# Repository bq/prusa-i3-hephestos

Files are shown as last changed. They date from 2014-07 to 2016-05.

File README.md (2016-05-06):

Prusa i3 Hephestos
======

In this repository you will find the source files for the [Prusa i3 Hephestos 3D printer](http://www.bq.com/es/productos/prusa-hephestos.html). If you are missing something, please do not hesitate to [file an issue on github](http://www.bq.com/es/productos/prusa-hephestos.html).

License 
======

Prusa i3 Hephestos is licensed under a [Creative Commons Attribution-ShareAlike 4.0 International License](http://creativecommons.org/licenses/by-sa/4.0/)

Firmware
===================

Sources on GitHub: https://github.com/bq/Marlin

Attributions
============
 
 - Josef Prusa: 
  - Prusa i3 3D printer original author.
 - Juan Gonzalez Gómez (Obijuan):
  - Desing "Final de carrera Eje X" and FreeCAD parts migration.
 - Manuel Palacios:
  - PowerCode 3D printer author. A lot of parts from this printer are used in Hephestos and derived("Eje X Carro A", "Anclaje del motor izquierdo del Eje Z", "Eje X izquierda").
 - Pedro de Oro Martín:
  - Desing; "Acople cadeneta Eje X", "Sujección final de carrera Eje Z", "Seguridad Hot End", "Soporte Ventilador", "Llave fija impresa".
 - Antonio Castro Gómez: 
  - Desing; "Sujección final de carrera Eje Y", "Soporte para filamento".
 - Jose Emilio Torres:
  - Desing "Soporte LCD".

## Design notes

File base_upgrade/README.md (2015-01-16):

Prusa i3 20x30cm bed upgrade kit
======

In this repository you will find the source files for the [Prusa i3 20x30cm bed upgrade kit](http://diwo.bq.com/amplia-tu-prusa-con-el-kit-de-actualizacion-a-base-larga/). If you are missing something, please do not hesitate to [file an issue on github](http://www.bq.com/es/productos/prusa-hephestos.html).

License 
======

Prusa i3 20x30cm bed upgrade kit is licensed under a [Creative Commons Attribution-ShareAlike 4.0 International License](http://creativecommons.org/licenses/by-sa/4.0/)

Attributions
============
 
 - Pedro de Oro Martín:
  - Kit author, Design drawings with LibreCAD , printed parts in OpenSCAD and modifications of parts pieces in OpenSCAD.
 - Josef Prusa:
  - Prusa i3 3D printer original author.
 - Manuel Palacios:
  - PowerCode 3D printer author of which have been derived parts; "Frontal de aluminio", "Tensor".
 - GalaCC authors:
  - Of which have been derived parts; "Posterior de aluminio", "Sujeta motor Y", which in turn have been derived from PowerCode 3D printer.
 - Federico Figueiredo de Sousa:
  - Author of the rendered images.

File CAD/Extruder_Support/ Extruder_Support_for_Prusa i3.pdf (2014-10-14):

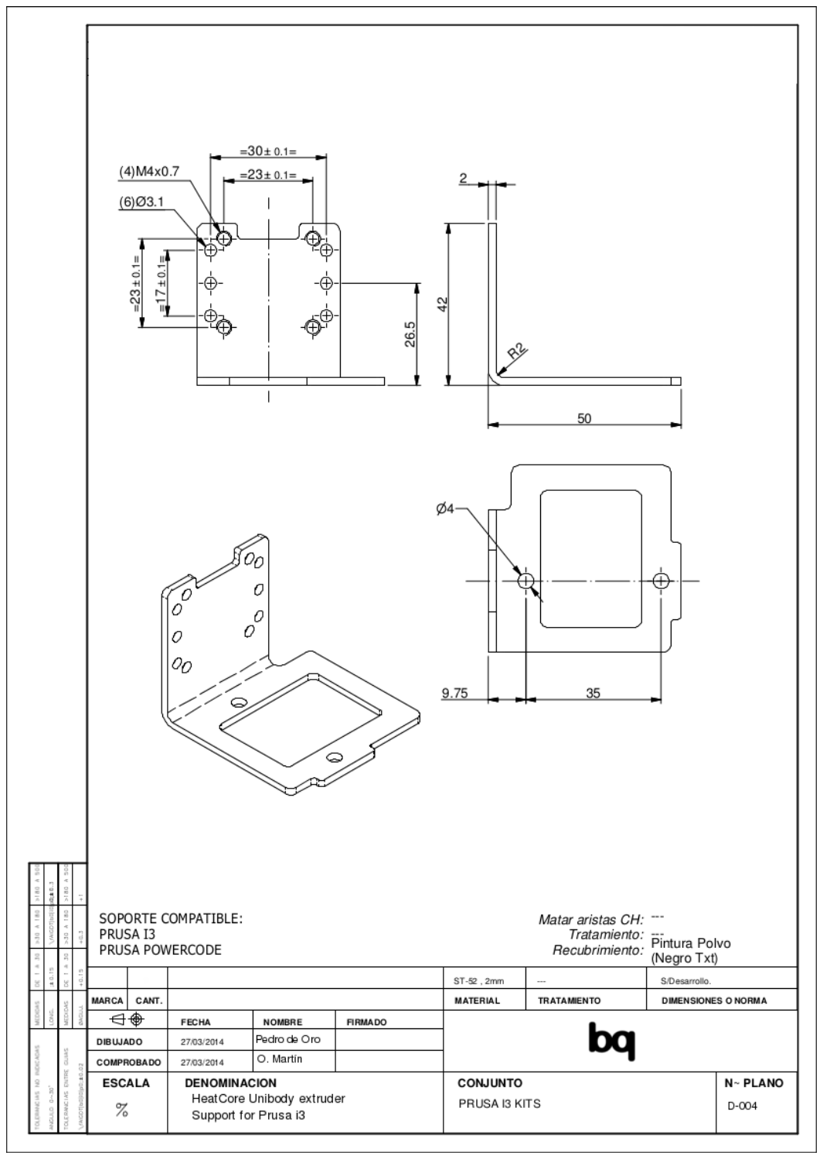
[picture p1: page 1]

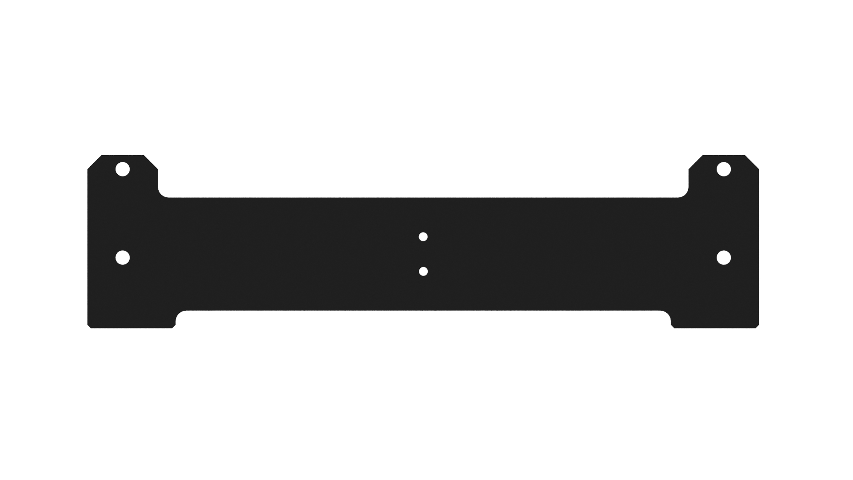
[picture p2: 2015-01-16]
base_upgrade/media/Posterior de Aluminio.jpg

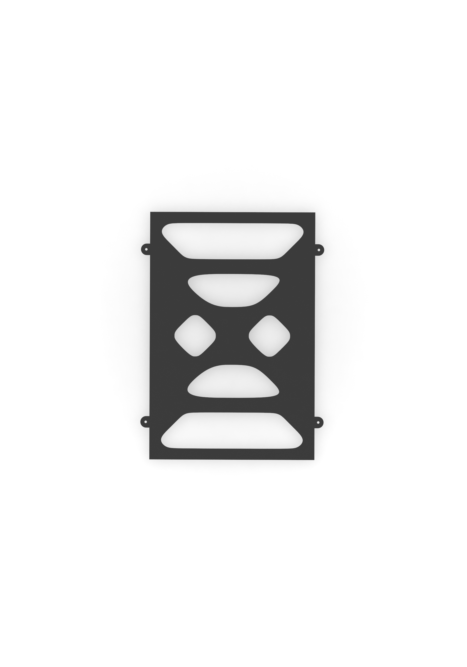
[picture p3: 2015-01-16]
base_upgrade/media/metacrilato.jpg

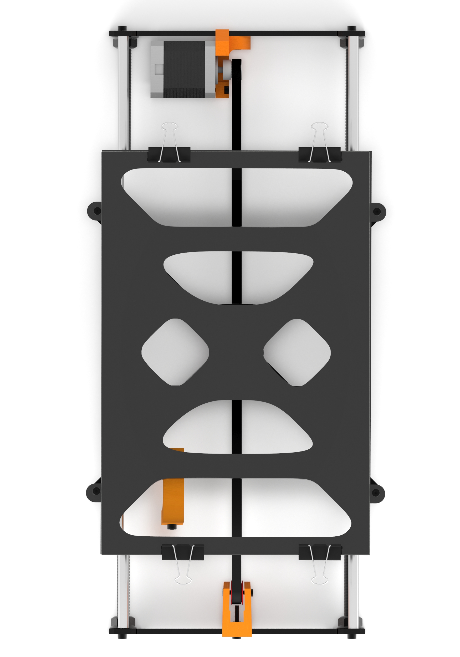
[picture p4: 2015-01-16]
base_upgrade/media/Base_larga_top.jpg

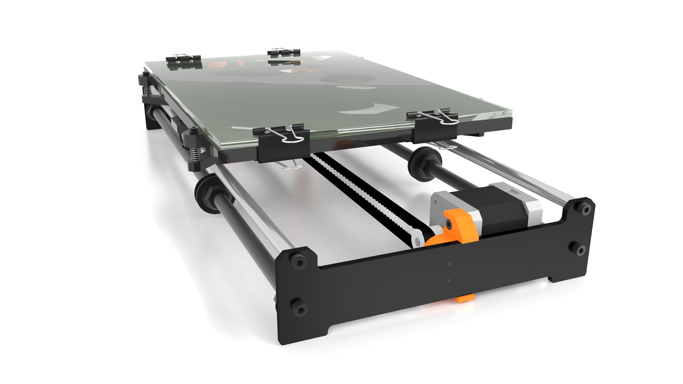
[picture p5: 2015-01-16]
base_upgrade/media/Base_larga_04n.jpg

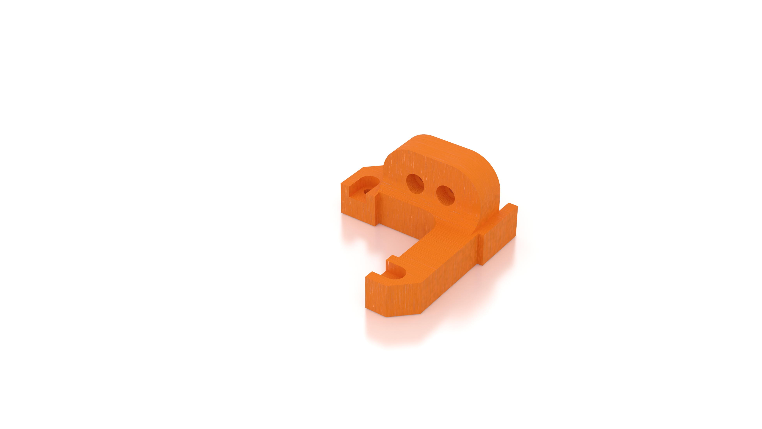
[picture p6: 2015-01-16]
base_upgrade/media/Pieza fijadora 2.jpg

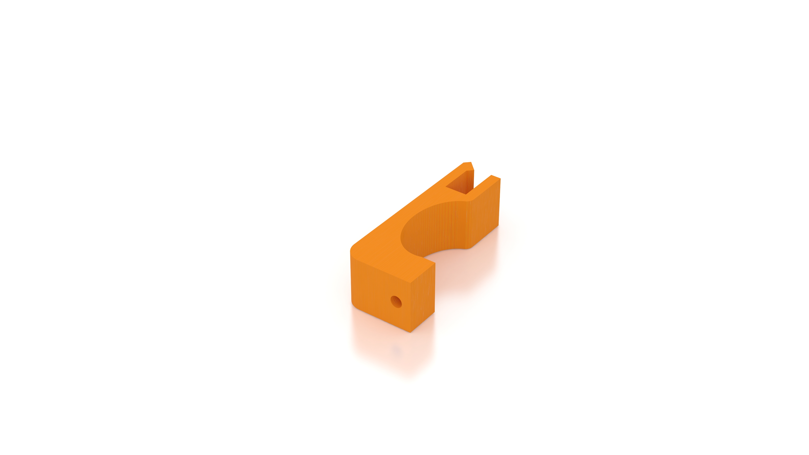
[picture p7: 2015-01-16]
base_upgrade/media/End-stop.jpg

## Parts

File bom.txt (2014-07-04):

BOM Prusa i3 Hephestos
======================

-----------Name------------------------------------------------------Quantity--

Allen key s/long Ø 2mm	                                                 1
ALLEN KEY S/LONG Ø2,5 FORUM	                                         1
Ceramic screw driver trimmer for electronics	                         1
Precision Needle 0.4mm diameter	                                         2
Printed tools: spanner and holder	                                 1
Ramps 1.4 Kit	                                                         1
Stepstick Drivers A49988 4 layers	                                 4
Mechanical Endstop	                                                 3
Smart LCD Controller	                                                 1
USB Cable 1.8m A-B	                                                 1
4 wire red blue green black (1 meter) for RAMPS	                         4
Nema 17 48 mm sin conector 42BYGHW811	                                 4
bq Direct Drive Extruder wiring kit 150 cm length	                 1
Bi-colour wire 2 x 1,5 mm	                                         0,15
AC/DC Power Adaptor SA1208 - 12V DC - 8A with 2.1mm Jack Connector	 1
SCHURTER 6003.0215 - Cable;	                                         1
2.1mm female Jack connector to two wires clam	                         1
Printed support for lcd, ramps and fan	                                 1
Tornillo M3x12 Screw - DIN-912 8.8 Class Black	                         4
M3 Nut - DIN 934 Class 8 Black	                                         38
Heat shrink tube 2.5 x 500 mm	                                         0,5
Black bridle 100 x 2.5 mm	                                         28
Brushless DC Cooling Fan - RD5010B12H	                                 1
Plastic Drag Chain Link 15x35 mm	                                 52
Marcha Direct Drive Extruder 1.75mm 0.4mm for RepRap Printers	         1
Witbox extruder Support for Prusa i3	                                 1
Tornillo M4 x 6 Din 7984	                                         2
M3x10 Screw - DIN-912 Class 8.8 Black	                                 35
Tornillo M3 x16 Screw - DIN-912 8.8 Class Black	                         8
M3x18 Screw - DIN-912 Class 8 Black	                                 2
Ø8X370MM-CROMAD Smooth rod	                                         2
M3x20 Screw - DIN-912 Class 8 Black	                                 9
Tornillo M3x25 Screw - DIN-912 8.8 Class Black	                         8
M6x40 Screw - DIN-912 Class 8.8 Black	                                 1
M5 Nut - DIN 934 Class 8 Black	                                         4
M6 Nut - DIN 934 Class 8 Black	                                         3
Printed x axis for Prusa i3	                                         1
Axial Ball Bearing 623zz	                                         2
GT2 Pulley 20 dientes	                                                 2
GT2 Timing Belt 6mm	                                                 2
Linear Ball Bearing LM8uu	                                         10
Ø8X340MM-CROMAD Smooth rod	                                         2
M10X370MM-NE Threaded rod	                                         2
M8X205MM Black transversal rod	                                         4
M8 Nut - DIN 934 Class 8 Black	                                         22
M10 Nut - DIN 934 Class 8 Black	                                         12
M8 Washer - DIN-125 Class 6 Black	                                 22
M10 Washer - DIN-125 Class 6 Black	                                 12
Printed y axis for Prusa i3	7
Aluminium Prusa i3 Frame and Bed 6mm black	1
22 x 22 x 10 mm acrylic printing bed for RepRap Printers	1
Standard Spring 30.5x4.5x0.45	4
Black binder clip	4
Ø8X320MM-CROMAD Smooth rod	2
M5X300MM-NE Threaded rod	2
Aluminium Flexible Shaft Coupling 5to5	2
Printed z axis for Prusa i3	
Glass 3mm 220x220 4EC 20x20	1
Jumper Wire (3 wires) with connectors – 40 cm	2
Jumper Wire (3 wires) with connectors – 85 cm	1
Hot End security	1
M10  Serrated Nut DIN 6923 Class 8 black	4
M10 Washer DIN 9021 Black (outter diameter 30mm)	4
Wire ferrule 1,5mm	4

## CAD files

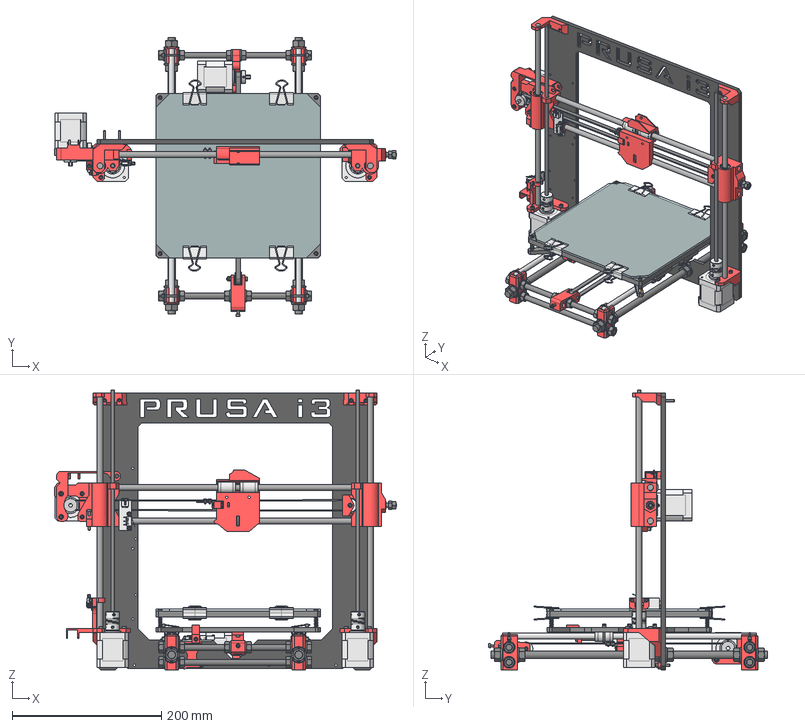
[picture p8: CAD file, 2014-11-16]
freecad/prusa-hephestos-assembly.fcstd
457.6 x 373.7 x 374.0 mm
M3x20-hex-bolt
M8-washer-tensor-1
M8-washer-tensor-2
M8-nut-tensor-1
M8-nut-tensor-2
belt-guide
M3-nut-y-tensor-003
M3-nut-y-tensor-2
M3x25-hex-bolt-1
M3-nut-y-tensor-1
y-idler-tensioner-final
y-Pulley-GT2
M3x10-bolt-motor-1
M3x10-bolt-motor-002
M3x10-bolt-motor-003
M3-setscrew-y-motor
y-Nema-17_Stepper_Motor_47mm
y-motor-plate
M8-washer-motor-1
M8-washer-motor-002
M8-washer-motor-003
M8-washer-motor-004
M8-nut-motor-1
M8-nut-motor-002
M8-nut-motor-003
M8-nut-motor-004
M10x370mm-left
M10x370mm-right
M8x340-smooth-rod-y-left
M8x340-smooth-rod-y-right
M8-washer-1
M8-washer-2
M8-washer-003
M8-washer-004
M8-washer-005
M8-washer-006
M8-washer-007
M8-washer-008
M8-washer-009
M8-washer-010
M8-washer-011
M8-washer-012
M8-washer-013
M8-washer-014
M8-washer-015
M8-washer-016
Washer-M10
Washer-M011
Washer-M012
Washer-M013
Washer-M014
Washer-M015
Washer-M016
Washer-M017
M8-nut-1
M8-nut-002
M8-nut-003
M8-nut-004
M8-nut-005
M8-nut-006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

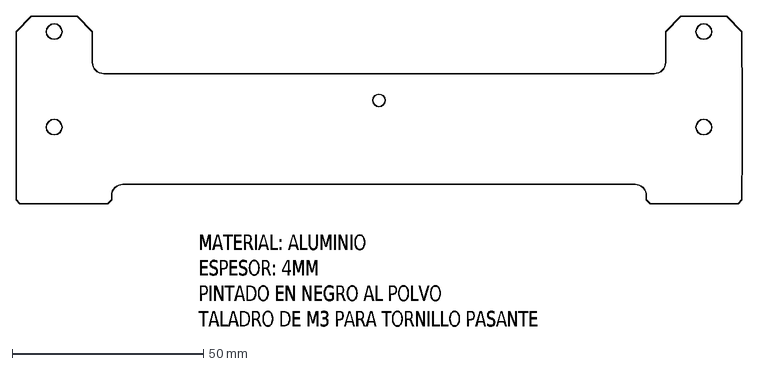
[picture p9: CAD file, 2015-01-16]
base_upgrade/DXF/Frontal_Alumino_4mm_Negro.dxf
MATERIAL: ALUMINIO ESPESOR: 4MM PINTADO EN NEGRO AL POLVO TALADRO DE M3 PARA TORNILLO PASANTE

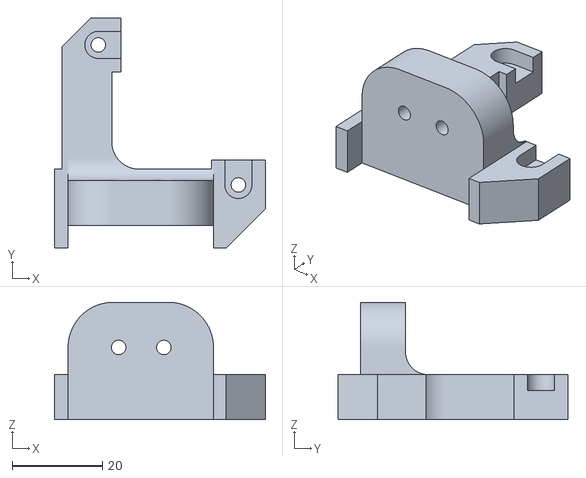
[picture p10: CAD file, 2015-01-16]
base_upgrade/STL/Sujeta_motor_base larga.stl
46.7 x 51.0 x 26.0

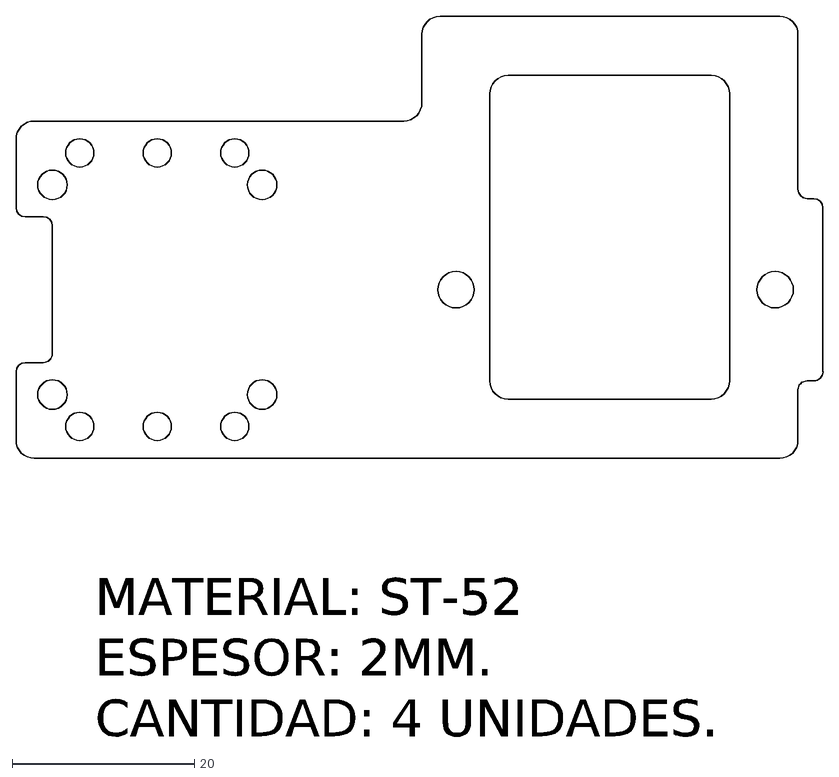
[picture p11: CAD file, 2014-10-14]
CAD/Extruder_Support/Extruder_Support_for_Prusa_i3.dxf
MATERIAL: ST-52 ESPESOR: 2MM. CANTIDAD: 4 UNIDADES.

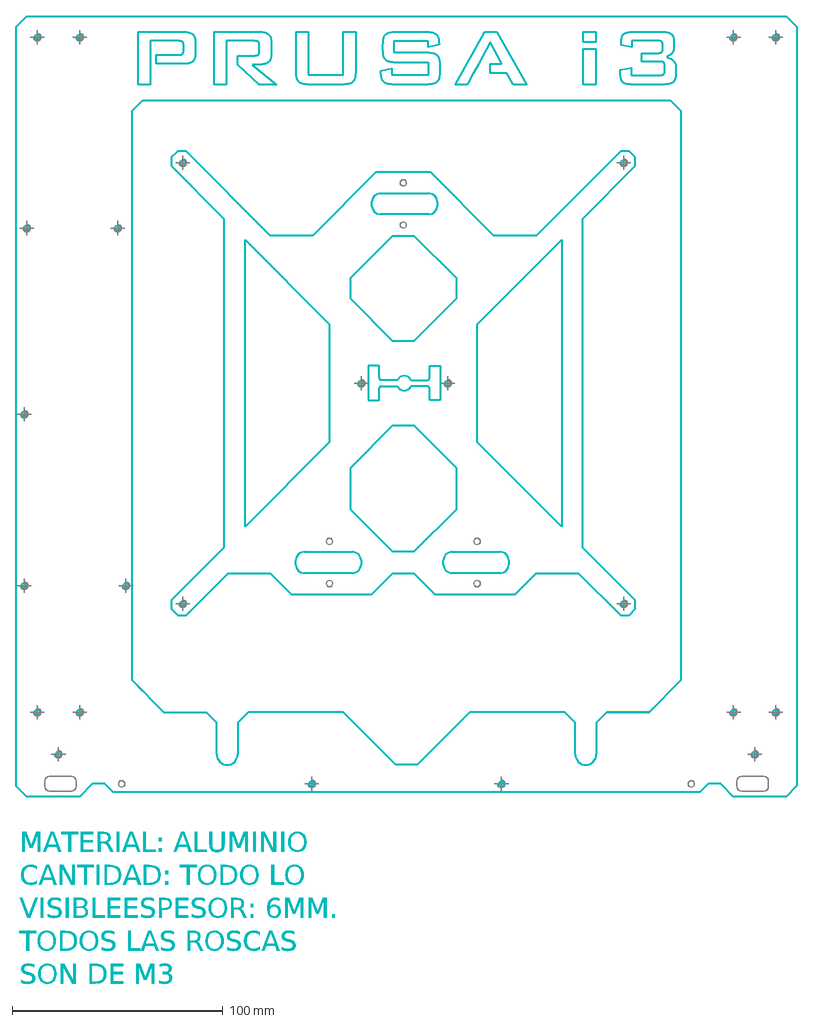
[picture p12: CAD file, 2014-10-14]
CAD/Frame&base/Frame&base_Hephestos_V2.dxf
MATERIAL: ALUMINIO CANTIDAD: TODO LO VISIBLE ESPESOR: 6MM. TODOS LAS ROSCAS SON DE M3

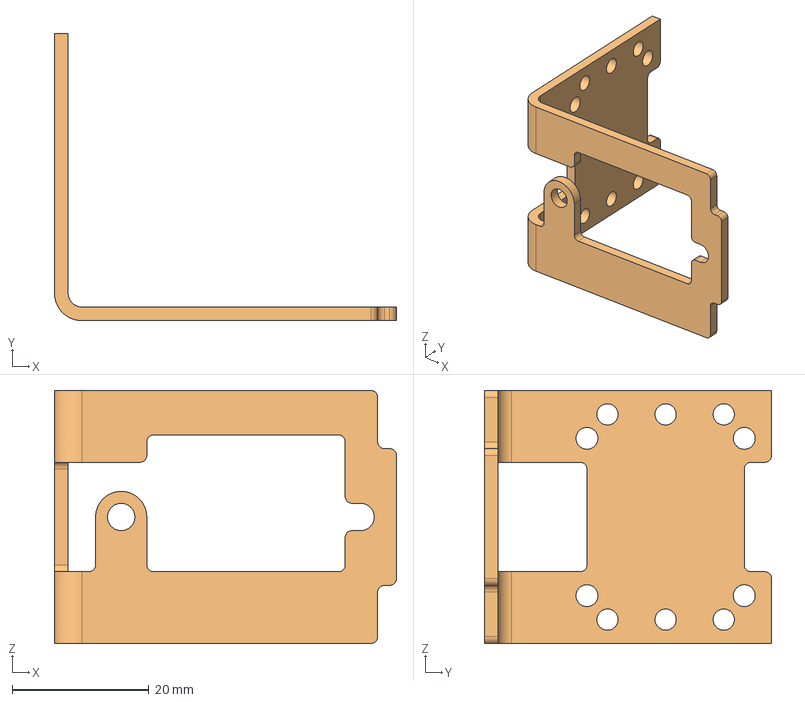
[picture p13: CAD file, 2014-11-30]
freecad/non-printable-parts/extruder-support.fcstd
50.0 x 42.0 x 37.0 mm
drills
extruder-support-final

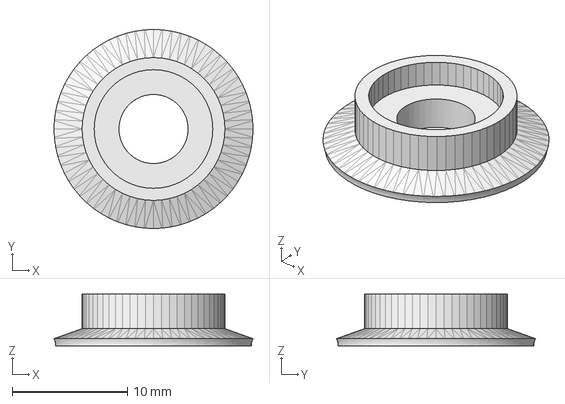
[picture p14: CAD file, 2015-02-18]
freecad/polea_V2.FCStd
17.3 x 17.3 x 4.50 mm

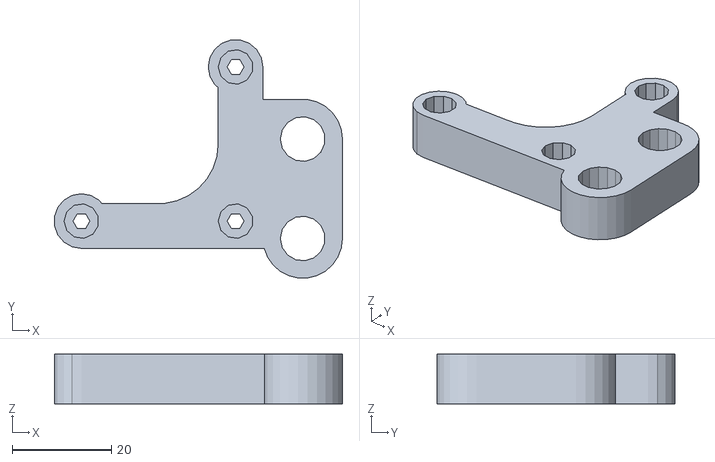
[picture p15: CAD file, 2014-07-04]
scad/Eje_Y/reinforced_y-motor/y-motor_mirror.stl
57.9 x 47.9 x 10.0

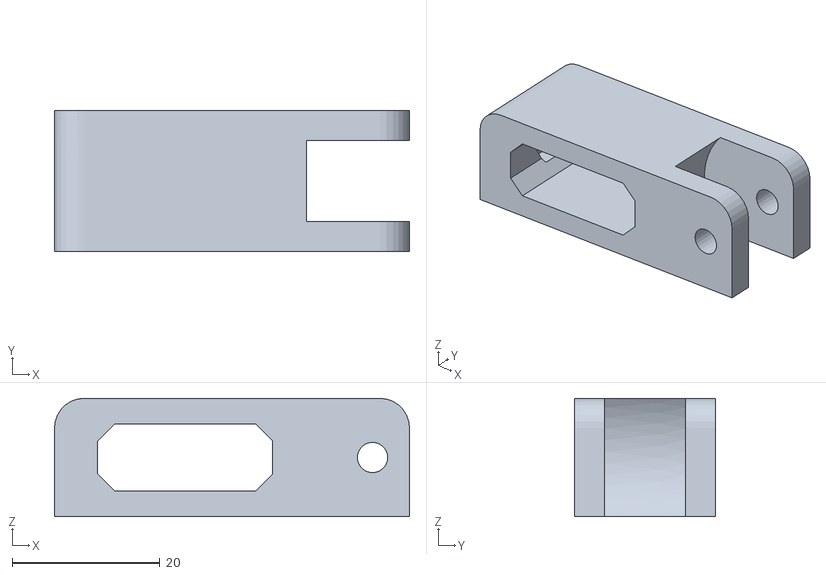
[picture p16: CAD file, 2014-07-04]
scad/Eje_Y/Y_tensor_correa/i3_y-idler_with_tensioner/i3_y-idler_with_tensioner/y-idler-tensioner3-4mm.stl
48.0 x 19.0 x 16.0

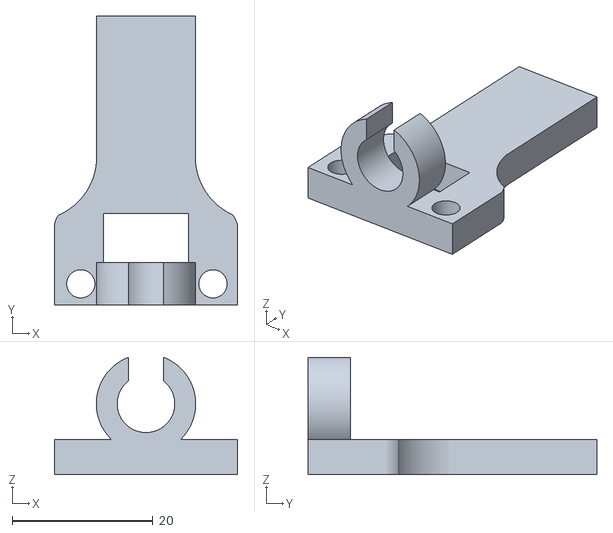
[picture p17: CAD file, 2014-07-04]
scad/Eje_Z/Final_de_carrera_eje Z/Eje_Z_final_carrera.stl
26.0 x 41.0 x 16.6

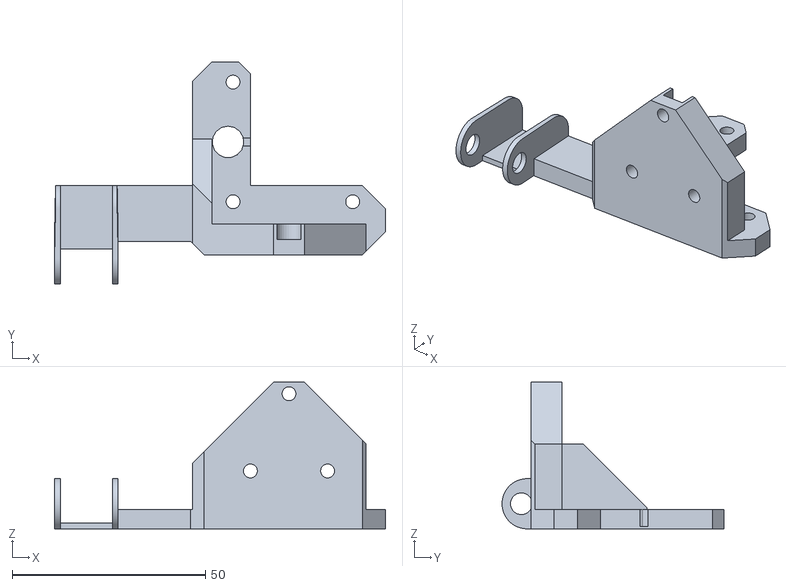
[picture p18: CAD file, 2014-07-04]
scad/Eje_Z/Pieza_motor_izquierdo_del_Eje Z/Eje_Z_soporte_inferior_izquierda.stl
85.8 x 57.5 x 38.0

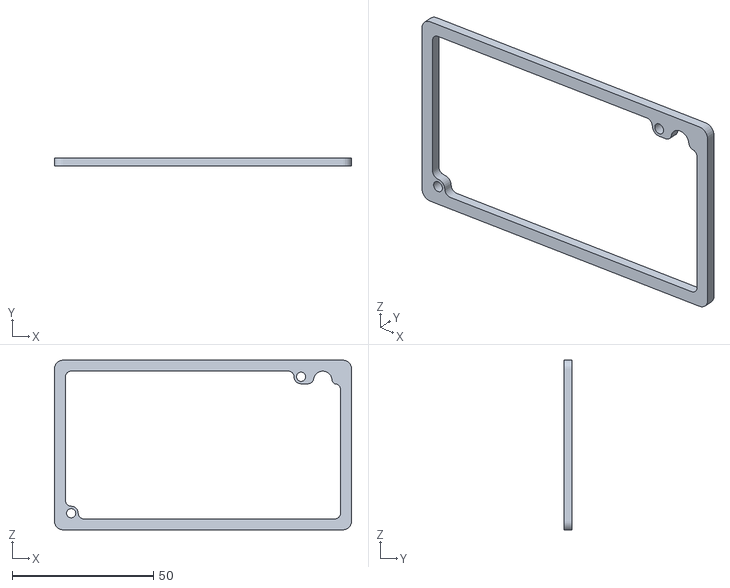
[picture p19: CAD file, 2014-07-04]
scad/Electronica/RAMPS_de_planos_de_witbox/suplemento_RAMPS.stl
105.0 x 3.00 x 60.0

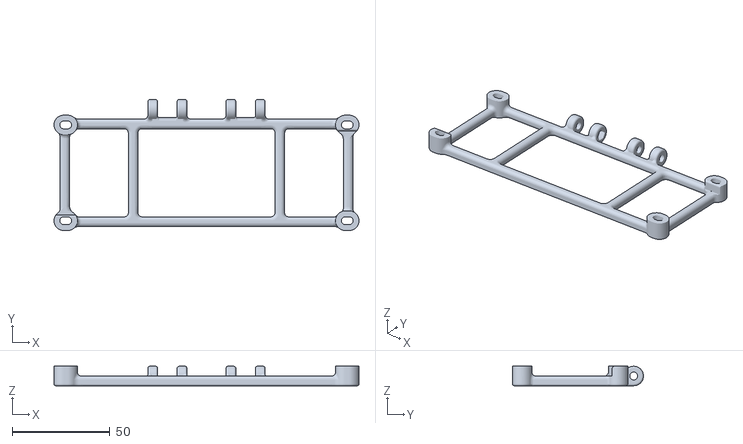
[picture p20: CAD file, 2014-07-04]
scad/Electronica/Soporte_LCD/Soporte_lcd.stl
156.0 x 67.0 x 10.0

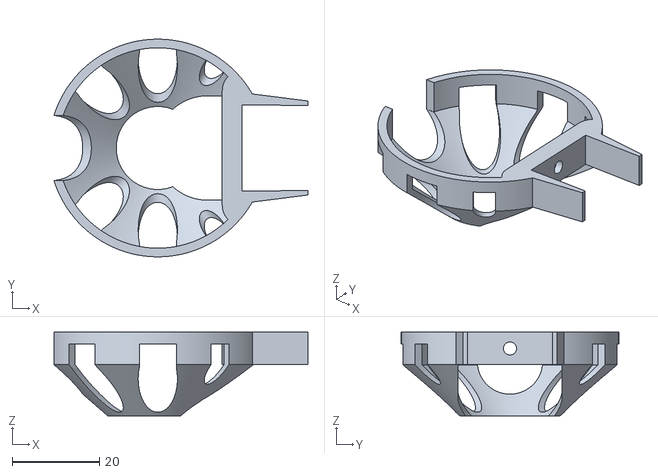
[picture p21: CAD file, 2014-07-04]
scad/Extrusor/Seguridad_Hot_End/Seguridad_Hot_End.stl
58.3 x 50.0 x 19.2

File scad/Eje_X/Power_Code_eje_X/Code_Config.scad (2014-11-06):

// Global configuration file of PowerCode
// By J.Rodigo (www.jra.so)
// Licence Creative commons atribution & share alike.
// Author: Mecano ( https://github.com/Mecan0/Code )

//************************************//
// Parámetros de configuración global //
//************************************//

$fn = 100;

// Cojinetes Lineales
dCoLi = 16.2 ;	// Diámetro

// Varillas lisas
dVaLi = 8.15 ; // Diámetro


//************************************//
//        Módulos de uso global       //
//************************************//

// Generar un hexágono circunscrito (Diámetro,altura) 
module hexagono(d,h){ 
	for (a = [0, 60,120]){ 
		rotate( a, [0, 0, 1])
		cube([d, d*tan(30), h], center = true);
	}
}

// Generar un cuadrado/chaflán a 45º (Arista,Altura,Giro{0 = 45º, 1 = 135º, ...}) 
module chamfer(a,h,g){ 
	rotate( g*90 + 45 , [0, 0, 1])
	cube([a, a, h]);
}

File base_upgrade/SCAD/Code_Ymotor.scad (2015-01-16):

// Created from Code_LevelExtruder.stl
// https://github.com/Mecan0/Code
// By J.Rodigo (www.jra.so)
// Licence Creative commons atribution & share alike.

include <Code_Config.scad>;

/**************************/
// Parámetros de la pieza  /
/**************************/

hBase = 10 ;	// Altura de la base (10)

dExtru = 40 ;	// Radio central del extrusor (40)

// Los dos taladros del soporte para el motor
dTaSo = 3.2 ;	// Diámetro del taladro (3.2)
dTaCh = 6 ; 	// Diámetro del zócalo (6)

dTor = 6.3 ; 	// Diámetro del tornillo del soporte (6.3)

module vaciadoEx(){
	// Vaciado exterior (Eje X)
	translate([3, -1, -1])
	cube([32.2, 6, hBase+2]);
	// Vaciado exterior (Eje Y)
	translate([-1, 17.5, -1]) 
	cube([2.7, 34, hBase+2]);
}

// Vaciado interior
module vaciadoIn(){
	translate([34, 19.5, -1])
	cube([14, 32, hBase+2]);
	translate([18.7, 17.5, -1])
	cube([16, 34, hBase+2]);
	translate([18.7, 23.5, -1])
	cylinder(h = hBase+2, r = 6);
	translate([12.7, 23.5, -1])
	cube([7, 15.5, hBase+2]);
	translate([14.7, 37, -1])
	cube([7, 14.5, hBase+2]);
}

// Chaflanes de la pieza en sentido anti-horario 
// empezando en por el del [0,0,0]
module chaflanes(){
	translate([0, 5, -1])
	chamfer(6, hBase+2, 2);
	translate([37.2, 0, -1])
	chamfer(14, hBase+2, 3);
	translate([46.7, 17.5, -1])
	chamfer(3, hBase+2, 0);
	translate([34.7, 17.5, -1])
	chamfer(3, hBase+2, 0);
	translate([12.7, 39, -1])
	chamfer(3, hBase+2, 3);
	translate([12.7, 51, -1])
	chamfer(3, hBase+2, 3);
	translate([1.7, 47, -1])
	chamfer(6, hBase+2, 0);
	translate([1.7, 17.5, -1])
	chamfer(3, hBase+2, 1);
}

// Taladro y zócalo para los tornillos de soporte del motor
module TMotor(){
	// Taladro para el tornillo
	cylinder(h = hBase+2, r = dTaSo/2, $fn=100);
	// Vaciado para la cabeza
	translate([0, 0, 7.5])
	cylinder(h = hBase-5.5, r = dTaCh/2, $fn=100);
	translate([0, -dTaCh/2, 7.5])
	cube([6, dTaCh, hBase-5.5]);
}

// Redondeo grande entre la sujeción y soporte
module redondeo(){
	difference(){
		// Relleno
		translate([3, 15, hBase])
		cube([16, 5, 5]);
		// Vaciado
		translate([2, 20, hBase+5])
		rotate( 90, [0, 1, 0])
		cylinder(h = 18, r = 5, $fn=100);	
	}
}

// Base de la pieza en el plano X-Y
module base(){
	difference(){
		union(){
			// Base de la pieza
			cube([46.7, 51, hBase]);
			// Redondeo entre la base y la sujecion
			redondeo();
		}
		union(){
			vaciadoEx();
			vaciadoIn();
			chaflanes();
			// Taladro de soporte del motor en el eje Y
			translate([9.7, 45, -1])
			TMotor();
			// Taladro de soporte del motor en el eje X
			translate([40.7, 14, -1])
			rotate( 90, [0, 0, 1])
			TMotor();
		}
	}
}

// Bloque de sujeción en el plano X-Z
module sujecion(){
	// Comando hull para unir todas las superficies 
	hull(){
		// Cilindros superiores
		translate([10, 0, 16])
		rotate( -90, [1, 0, 0])
		cylinder(h = 10, r = 10, $fn=100);
		translate([22.2, 0, 16])
		rotate( -90, [1, 0, 0])
		cylinder(h = 10, r = 10, $fn=100);
		// Cubo de la base
		cube([32.2, 10, 1]);
	}
}

// Vaciado y taladro para el tornillo de sujeción
module TTornillo(){
	// Taladro para el tornillo
	translate([22.2, -1, 16])
	rotate( -90, [1, 0, 0])
	cylinder(h = 9, r = dTor/2, $fn=100);
	// Vaciado para la cabeza 
	translate([22.2, 7, 16])
	rotate( -90, [1, 0, 0])
	cylinder(h = 6, r = 9, $fn=100);	
	translate([13.2, 7, 16])
	cube([18, 6, 18]);
	// Redondeo pequeño
	hull(){
		translate([25, 10, hBase+3])
		rotate( 90, [0, 1, 0])
		cylinder(h = 10, r = 3, $fn=100);
		translate([25, 7, hBase+3])
		cube([10, 6, 10]);
	}
}


// Unimos todos los bloques para crear la pieza
module pieza(){
	difference(){
		union(){
			// Base de la pieza
			base();
			// Soporte para el tornillo
			translate([3, 5, hBase-10])
			sujecion();
		}
		union(){
			// Taladro y zocalo para el tornillo del soporte
			translate([3, 5, 0])
			TTornillo();
		}
	}
}

// Generamos la pieza!!

	pieza();

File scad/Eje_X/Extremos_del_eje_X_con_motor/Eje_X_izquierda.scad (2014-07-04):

//---------------------------------------------------------------
//--  Eje X izquierda.  (c) Antonio Castro Gómez
//---------------------------------------------------------------
//-- Released under the GPL license
//---------------------------------------------------------------


module object1(scale) {polyhedron(
 points=[[4.721688e+001,-5.000000e+000,3.250000e+001],[4.721688e+001,-8.500000e+000,3.250000e+001],[4.173205e+001,-5.000000e+000,4.200000e+001],[4.173205e+001,-5.000000e+000,4.200000e+001],[4.721688e+001,-8.500000e+000,3.250000e+001],[4.000000e+001,-8.500000e+000,4.500000e+001],[4.173205e+001,-5.000000e+000,4.200000e+001],[4.000000e+001,-8.500000e+000,4.500000e+001],[4.000000e+001,-2.000000e+000,4.500000e+001],[4.000000e+001,-8.500000e+000,1.500000e+001],[4.721688e+001,-8.500000e+000,2.750000e+001],[4.000000e+001,-5.000000e+000,1.500000e+001],[4.000000e+001,-5.000000e+000,1.500000e+001],[4.721688e+001,-8.500000e+000,2.750000e+001],[4.721688e+001,-5.000000e+000,2.750000e+001],[5.450000e+001,-8.500000e+000,8.000000e+000],[4.758521e+001,-8.500000e+000,3.171010e+001],[4.781079e+001,-8.500000e+000,3.086824e+001],[5.450000e+001,-8.500000e+000,8.000000e+000],[4.781079e+001,-8.500000e+000,3.086824e+001],[4.788675e+001,-8.500000e+000,3.000000e+001],[5.450000e+001,-8.500000e+000,8.000000e+000],[4.788675e+001,-8.500000e+000,3.000000e+001],[4.781079e+001,-8.500000e+000,2.913176e+001],[5.450000e+001,-8.500000e+000,8.000000e+000],[4.781079e+001,-8.500000e+000,2.913176e+001],[4.758521e+001,-8.500000e+000,2.828990e+001],[5.450000e+001,-8.500000e+000,8.000000e+000],[4.758521e+001,-8.500000e+000,2.828990e+001],[4.721688e+001,-8.500000e+000,2.750000e+001],[5.450000e+001,-8.500000e+000,8.000000e+000],[4.721688e+001,-8.500000e+000,2.750000e+001],[4.000000e+001,-8.500000e+000,1.500000e+001],[5.450000e+001,-8.500000e+000,8.000000e+000],[4.000000e+001,-8.500000e+000,1.500000e+001],[4.000000e+001,-8.500000e+000,8.000000e+000],[5.450000e+001,-8.500000e+000,5.800000e+001],[4.000000e+001,-8.500000e+000,5.800000e+001],[4.000000e+001,-8.500000e+000,4.500000e+001],[5.450000e+001,-8.500000e+000,5.800000e+001],[4.000000e+001,-8.500000e+000,4.500000e+001],[4.721688e+001,-8.500000e+000,3.250000e+001],[5.450000e+001,-8.500000e+000,5.800000e+001],[4.721688e+001,-8.500000e+000,3.250000e+001],[4.758521e+001,-8.500000e+000,3.171010e+001],[5.450000e+001,-8.500000e+000,5.800000e+001],[4.758521e+001,-8.500000e+000,3.171010e+001],[5.450000e+001,-8.500000e+000,8.000000e+000],[4.721688e+001,-5.000000e+000,3.250000e+001],[4.173205e+001,-5.000000e+000,4.200000e+001],[7.535000e+001,-5.000000e+000,1.500000e+001],[4.721688e+001,-5.000000e+000,3.250000e+001],[7.535000e+001,-5.000000e+000,1.500000e+001],[4.758521e+001,-5.000000e+000,3.171010e+001],[7.535000e+001,-5.000000e+000,1.500000e+001],[4.000000e+001,-5.000000e+000,1.500000e+001],[4.721688e+001,-5.000000e+000,2.750000e+001],[7.535000e+001,-5.000000e+000,1.500000e+001],[4.721688e+001,-5.000000e+000,2.750000e+001],[4.758521e+001,-5.000000e+000,2.828990e+001],[7.535000e+001,-5.000000e+000,1.500000e+001],[4.758521e+001,-5.000000e+000,2.828990e+001],[4.781079e+001,-5.000000e+000,2.913176e+001],[7.535000e+001,-5.000000e+000,1.500000e+001],[4.781079e+001,-5.000000e+000,2.913176e+001],[4.788675e+001,-5.000000e+000,3.000000e+001],[7.535000e+001,-5.000000e+000,1.500000e+001],[4.788675e+001,-5.000000e+000,3.000000e+001],[4.781079e+001,-5.000000e+000,3.086824e+001],[7.535000e+001,-5.000000e+000,1.500000e+001],[4.781079e+001,-5.000000e+000,3.086824e+001],[4.758521e+001,-5.000000e+000,3.171010e+001],[8.000000e+001,-5.000000e+000,4.035000e+001],[9.383604e+001,-5.000000e+000,4.035000e+001],[9.250000e+001,-5.000000e+000,3.803590e+001],[8.000000e+001,-5.000000e+000,4.035000e+001],[9.250000e+001,-5.000000e+000,3.803590e+001],[8.188490e+001,-5.000000e+000,1.965000e+001],[8.000000e+001,-5.000000e+000,4.035000e+001],[8.188490e+001,-5.000000e+000,1.965000e+001],[8.000000e+001,-5.000000e+000,1.965000e+001],[8.000000e+001,-5.000000e+000,4.035000e+001],[8.000000e+001,-5.000000e+000,1.965000e+001],[7.535000e+001,-5.000000e+000,1.500000e+001],[8.000000e+001,-5.000000e+000,4.035000e+001],[7.535000e+001,-5.000000e+000,1.500000e+001],[4.173205e+001,-5.000000e+000,4.200000e+001],[8.000000e+001,-5.000000e+000,4.035000e+001],[4.173205e+001,-5.000000e+000,4.200000e+001],[8.000000e+001,-5.000000e+000,4.200000e+001],[4.721688e+001,-5.000000e+000,2.750000e+001],[4.721688e+001,-8.500000e+000,2.750000e+001],[4.758521e+001,-5.000000e+000,2.828990e+001],[4.758521e+001,-5.000000e+000,2.828990e+001],[4.721688e+001,-8.500000e+000,2.750000e+001],[4.758521e+001,-8.500000e+000,2.828990e+001],[4.758521e+001,-5.000000e+000,2.828990e+001],[4.758521e+001,-8.500000e+000,2.828990e+001],[4.781079e+001,-5.000000e+000,2.913176e+001],[4.781079e+001,-5.000000e+000,2.913176e+001],[4.758521e+001,-8.500000e+000,2.828990e+001],[4.781079e+001,-8.500000e+000,2.913176e+001],[4.781079e+001,-5.000000e+000,2.913176e+001],[4.781079e+001,-8.500000e+000,2.913176e+001],[4.788675e+001,-5.000000e+000,3.000000e+001],[4.788675e+001,-5.000000e+000,3.000000e+001],[4.781079e+001,-8.500000e+000,2.913176e+001],[4.788675e+001,-8.500000e+000,3.000000e+001],[4.788675e+001,-5.000000e+000,3.000000e+001],[4.788675e+001,-8.500000e+000,3.000000e+001],[4.781079e+001,-5.000000e+000,3.086824e+001],[4.781079e+001,-5.000000e+000,3.086824e+001],[4.788675e+001,-8.500000e+000,3.000000e+001],[4.781079e+001,-8.500000e+000,3.086824e+001],[4.781079e+001,-5.000000e+000,3.086824e+001],[4.781079e+001,-8.500000e+000,3.086824e+001],[4.758521e+001,-5.000000e+000,3.171010e+001],[4.758521e+001,-5.000000e+000,3.171010e+001],[4.781079e+001,-8.500000e+000,3.086824e+001],[4.758521e+001,-8.500000e+000,3.171010e+001],[4.758521e+001,-5.000000e+000,3.171010e+001],[4.758521e+001,-8.500000e+000,3.171010e+001],[4.721688e+001,-5.000000e+000,3.250000e+001],[4.721688e+001,-5.000000e+000,3.250000e+001],[4.758521e+001,-8.500000e+000,3.171010e+001],[4.721688e+001,-8.500000e+000,3.250000e+001],[4.000000e+001,5.000000e+000,1.500000e+001],[4.721688e+001,5.000000e+000,2.750000e+001],[4.000000e+001,8.500000e+000,1.500000e+001],[4.000000e+001,8.500000e+000,1.500000e+001],[4.721688e+001,5.000000e+000,2.750000e+001],[4.721688e+001,8.500000e+000,2.750000e+001],[4.173205e+001,5.000000e+000,4.200000e+001],[4.000000e+001,2.000000e+000,4.500000e+001],[4.000000e+001,8.500000e+000,4.500000e+001],[4.721688e+001,8.500000e+000,3.250000e+001],[4.173205e+001,5.000000e+000,4.200000e+001],[4.000000e+001,8.500000e+000,4.500000e+001],[4.721688e+001,5.000000e+000,3.250000e+001],[4.173205e+001,5.000000e+000,4.200000e+001],[4.721688e+001,8.500000e+000,3.250000e+001],[8.000000e+001,5.000000e+000,4.035000e+001],[9.250000e+001,5.000000e+000,3.803590e+001],[9.383604e+001,5.000000e+000,4.035000e+001],[7.535000e+001,5.000000e+000,1.500000e+001],[8.000000e+001,5.000000e+000,1.965000e+001],[8.000000e+001,5.000000e+000,4.035000e+001],[7.535000e+001,5.000000e+000,1.500000e+001],[8.000000e+001,5.000000e+000,4.035000e+001],[8.000000e+001,5.000000e+000,4.200000e+001],[7.535000e+001,5.000000e+000,1.500000e+001],[8.000000e+001,5.000000e+000,4.200000e+001],[4.173205e+001,5.000000e+000,4.200000e+001],[7.535000e+001,5.000000e+000,1.500000e+001],[4.173205e+001,5.000000e+000,4.200000e+001],[4.721688e+001,5.000000e+000,3.250000e+001],[7.535000e+001,5.000000e+000,1.500000e+001],[4.721688e+001,5.000000e+000,3.250000e+001],[4.758521e+001,5.000000e+000,3.171010e+001],[7.535000e+001,5.000000e+000,1.500000e+001],[4.758521e+001,5.000000e+000,3.171010e+001],[4.781079e+001,5.000000e+000,3.086824e+001],[7.535000e+001,5.000000e+000,1.500000e+001],[4.781079e+001,5.000000e+000,3.086824e+001],[4.788675e+001,5.000000e+000,3.000000e+001],[7.535000e+001,5.000000e+000,1.500000e+001],[4.788675e+001,5.000000e+000,3.000000e+001],[4.781079e+001,5.000000e+000,2.913176e+001],[7.535000e+001,5.000000e+000,1.500000e+001],[4.781079e+001,5.000000e+000,2.913176e+001],[4.758521e+001,5.000000e+000,2.828990e+001],[7.535000e+001,5.000000e+000,1.500000e+001],[4.758521e+001,5.000000e+000,2.828990e+001],[4.721688e+001,5.000000e+000,2.750000e+001],[7.535000e+001,5.000000e+000,1.500000e+001],[4.721688e+001,5.000000e+000,2.750000e+001],[4.000000e+001,5.000000e+000,1.500000e+001],[8.000000e+001,5.000000e+000,1.965000e+001],[9.389810e+001,5.000000e+000,1.965000e+001],[9.330056e+001,5.000000e+000,2.050570e+001],[8.000000e+001,5.000000e+000,1.965000e+001],[9.330056e+001,5.000000e+000,2.050570e+001],[9.286034e+001,5.000000e+000,2.145200e+001],[8.000000e+001,5.000000e+000,1.965000e+001],[9.286034e+001,5.000000e+000,2.145200e+001],[9.259077e+001,5.000000e+000,2.246027e+001],[8.000000e+001,5.000000e+000,1.965000e+001],[9.259077e+001,5.000000e+000,2.246027e+001],[9.250000e+001,5.000000e+000,2.350000e+001],[8.000000e+001,5.000000e+000,1.965000e+001],[9.250000e+001,5.000000e+000,2.350000e+001],[9.250000e+001,5.000000e+000,3.803590e+001],[8.000000e+001,5.000000e+000,1.965000e+001],[9.250000e+001,5.000000e+000,3.803590e+001],[8.000000
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

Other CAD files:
scad/Eje_Y/Y_tensor_correa/y-idler-tensioner3-3mm.stl
scad/Extrusor/Tobera_witbox/Tobera_05.stl
scad/Herramientas/bq-logo2d.dxf
step/01-Eje_X_acople_cadeneta_izquierda_v3.stp
base_upgrade/SCAD/Code_Ymotor_modificado.scad
CAD/Frame&base/Frame&base_Hephestos.dxf
base_upgrade/DXF/Base_metacrialto_8mm_Negro.dxf
base_upgrade/DXF/Cristal_base_larga_Prusa_i3.dxf
base_upgrade/DXF/Posterior_Aluminio_4mm_Negro.dxf
base_upgrade/DXF/Varilla_M10x440mm_roscada_negra_con_rosca_interior_M4x12mm.dxf
base_upgrade/DXF/Varilla_lisa_M8_rosca_interior_M4x12mm.dxf
base_upgrade/SCAD/Code_Yidler_623_modificado.scad
base_upgrade/SCAD/EjeY_final_carrera_base_larga.scad
base_upgrade/SCAD/Sujeta_cristal.scad
base_upgrade/STL/Code_Yidler_623_modificado.stl
base_upgrade/STL/Code_Ymotor_modificado.stl
base_upgrade/STL/EjeY_final_carrera_base_larga.stl
base_upgrade/STL/Frontal_base_larga.stl
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

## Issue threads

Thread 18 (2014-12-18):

TODO attributions

AndrewBCN, 2014-12-18:
Hola,
Se escribe Attributions y no Atributions!
Y para las Proteinas, creo que los autores son Josef Prusa, Misan, J Rodrigo y Obijuan (y probablemente otros que no conozco).
Gracias,
Saludos,
Andre

Closed 2015-01-16.

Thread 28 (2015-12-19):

Firmware link

Serveurperso, 2015-12-19:
Hello, irmware src link doesn't work.

Firmware: https://github.com/bq/Marlin/tree/v1.4_hephestos

Serveurperso, 2015-12-19:
Found here https://github.com/bq/Marlin

Closed 2015-12-19.

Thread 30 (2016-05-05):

don't work firmware download link

echadow, 2016-05-05:
don't work firmware download link.

sinuso, 2016-05-06:
On page bq support it does not appear. On page in Spanish if.
http://www.bq.com/es/support/prusa

echadow, 2016-05-06:
thx but i need the firmware in .ino. bq only have the .hex

mtowara, 2016-05-06:
It's now here:
https://github.com/bq/Marlin

sinuso, 2016-05-06:
@mtowara There is no compiled firmware or the ino

mtowara, 2016-05-06:
Yeah, it looks like they removed the ino file, but its still the Marlin src and you can compile it with Arduino using the Makefile

ivan-galvez, 2016-05-06:
The firmware development sources are maintained on GitHub: https://github.com/bq/Marlin

From version 2.0.0, onwards .ino format file has been dropped. If you want to compile the sources by yourself, you will need to use the provided GNU Makefile. Please refer to the Documentation notes, regarding how to compile the code.

If you want the latest stable release for BQ Prusa i3 Hephestos, you will need to download version 1.4.2. This version still keeps support for .ino files. Sources are accessible from the Releases/Tags page on GitHub: https://github.com/bq/Marlin/releases/tag/1.4.2

sinuso, 2016-05-06:
Gracias @ivan-galvez. El que no sepa ingles ni compilar, le va a tocar sudar xD

echadow, 2016-05-06:
hablas español?

Closed 2016-05-06.

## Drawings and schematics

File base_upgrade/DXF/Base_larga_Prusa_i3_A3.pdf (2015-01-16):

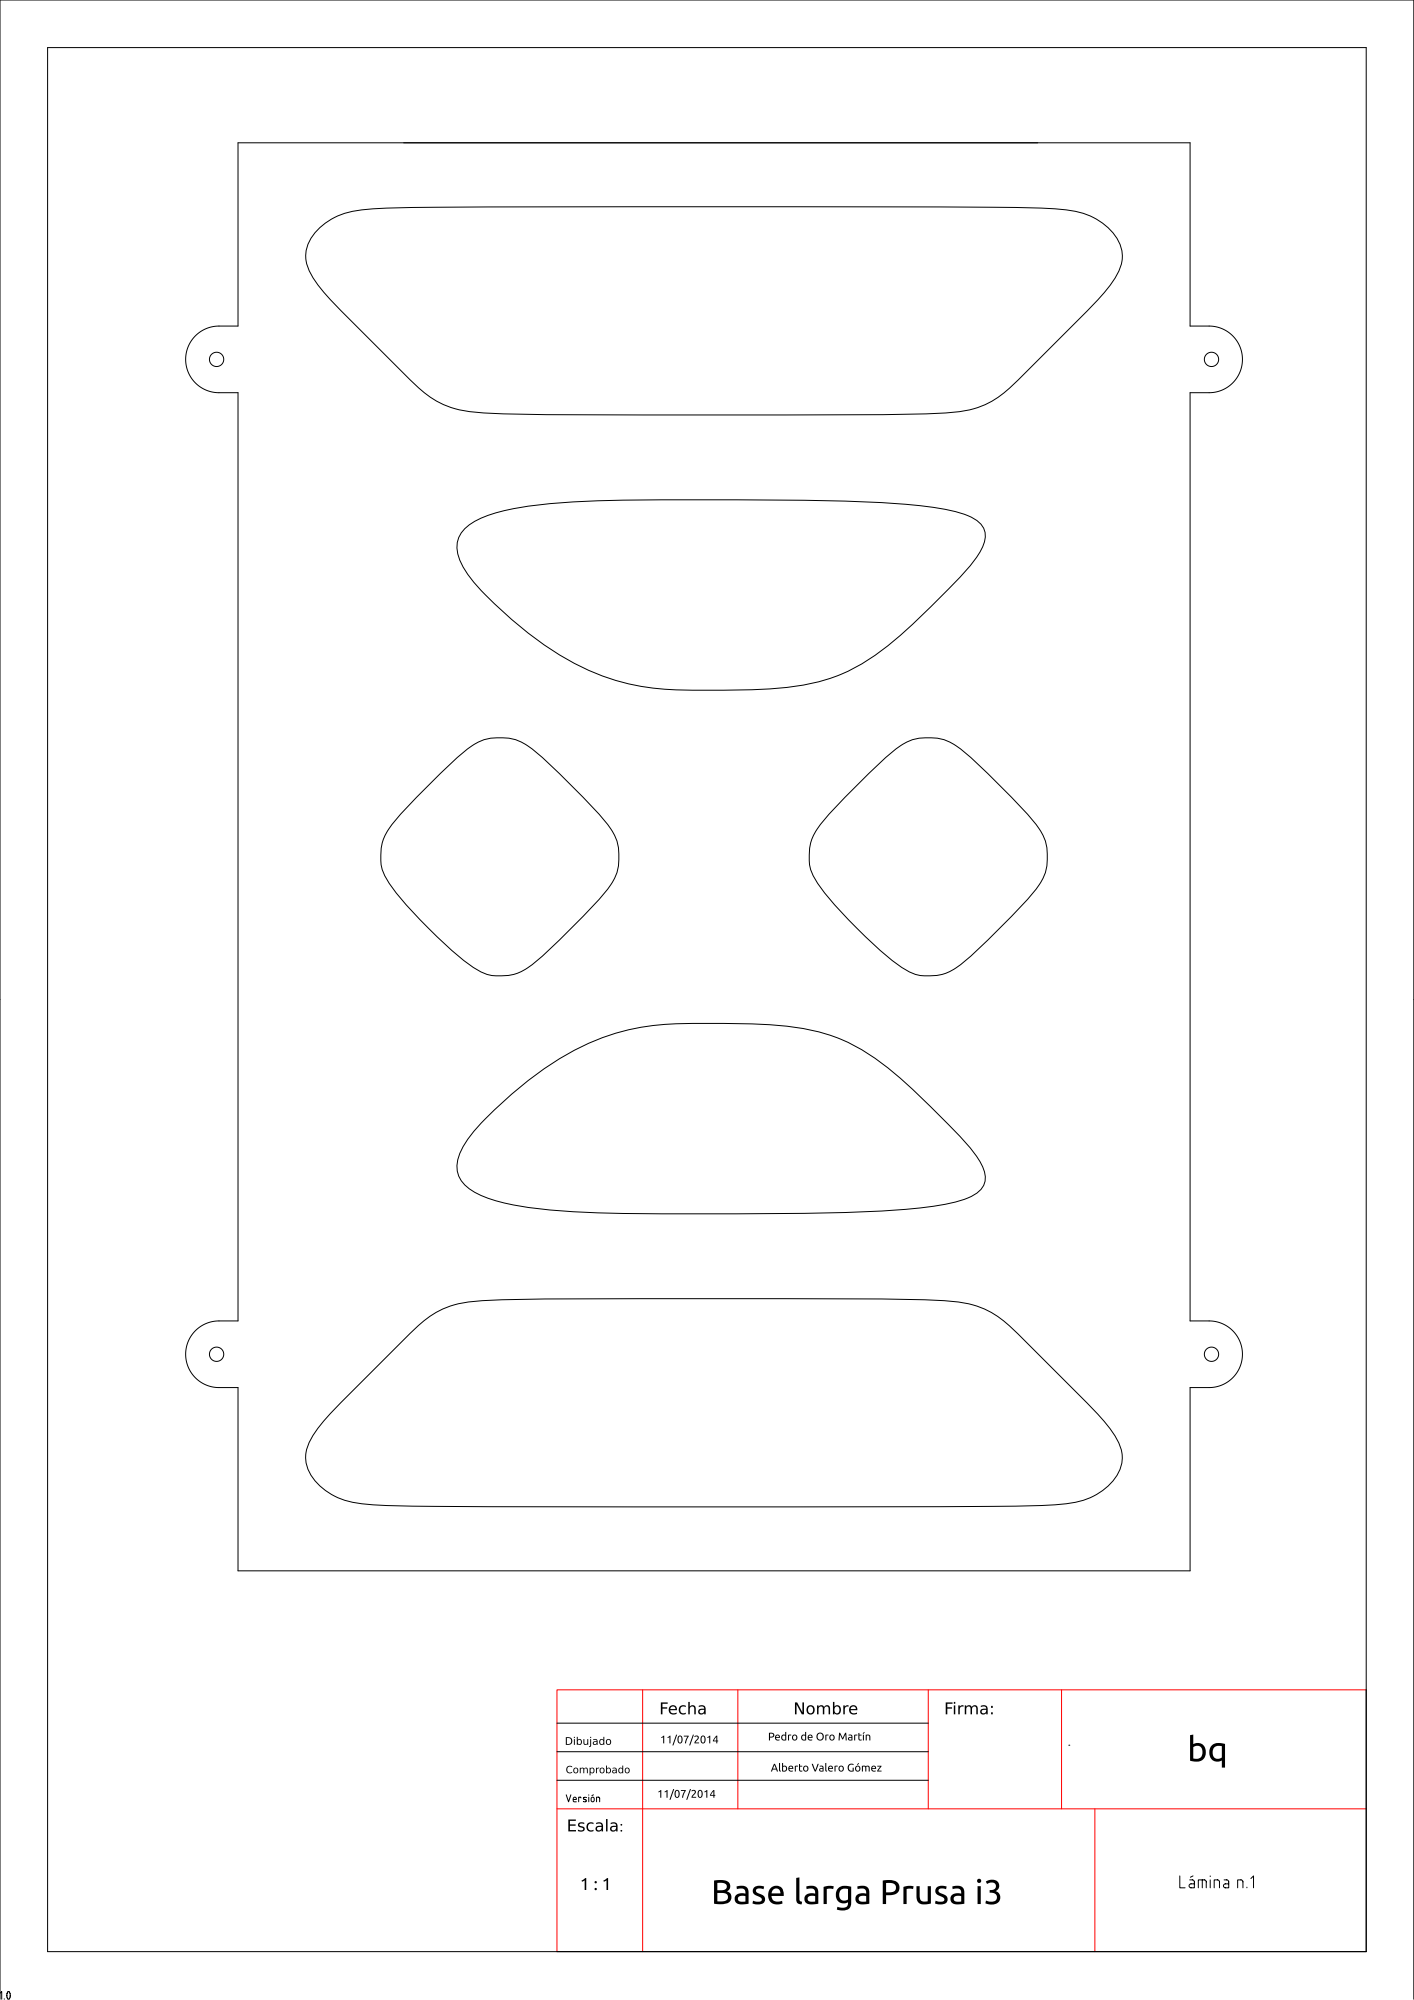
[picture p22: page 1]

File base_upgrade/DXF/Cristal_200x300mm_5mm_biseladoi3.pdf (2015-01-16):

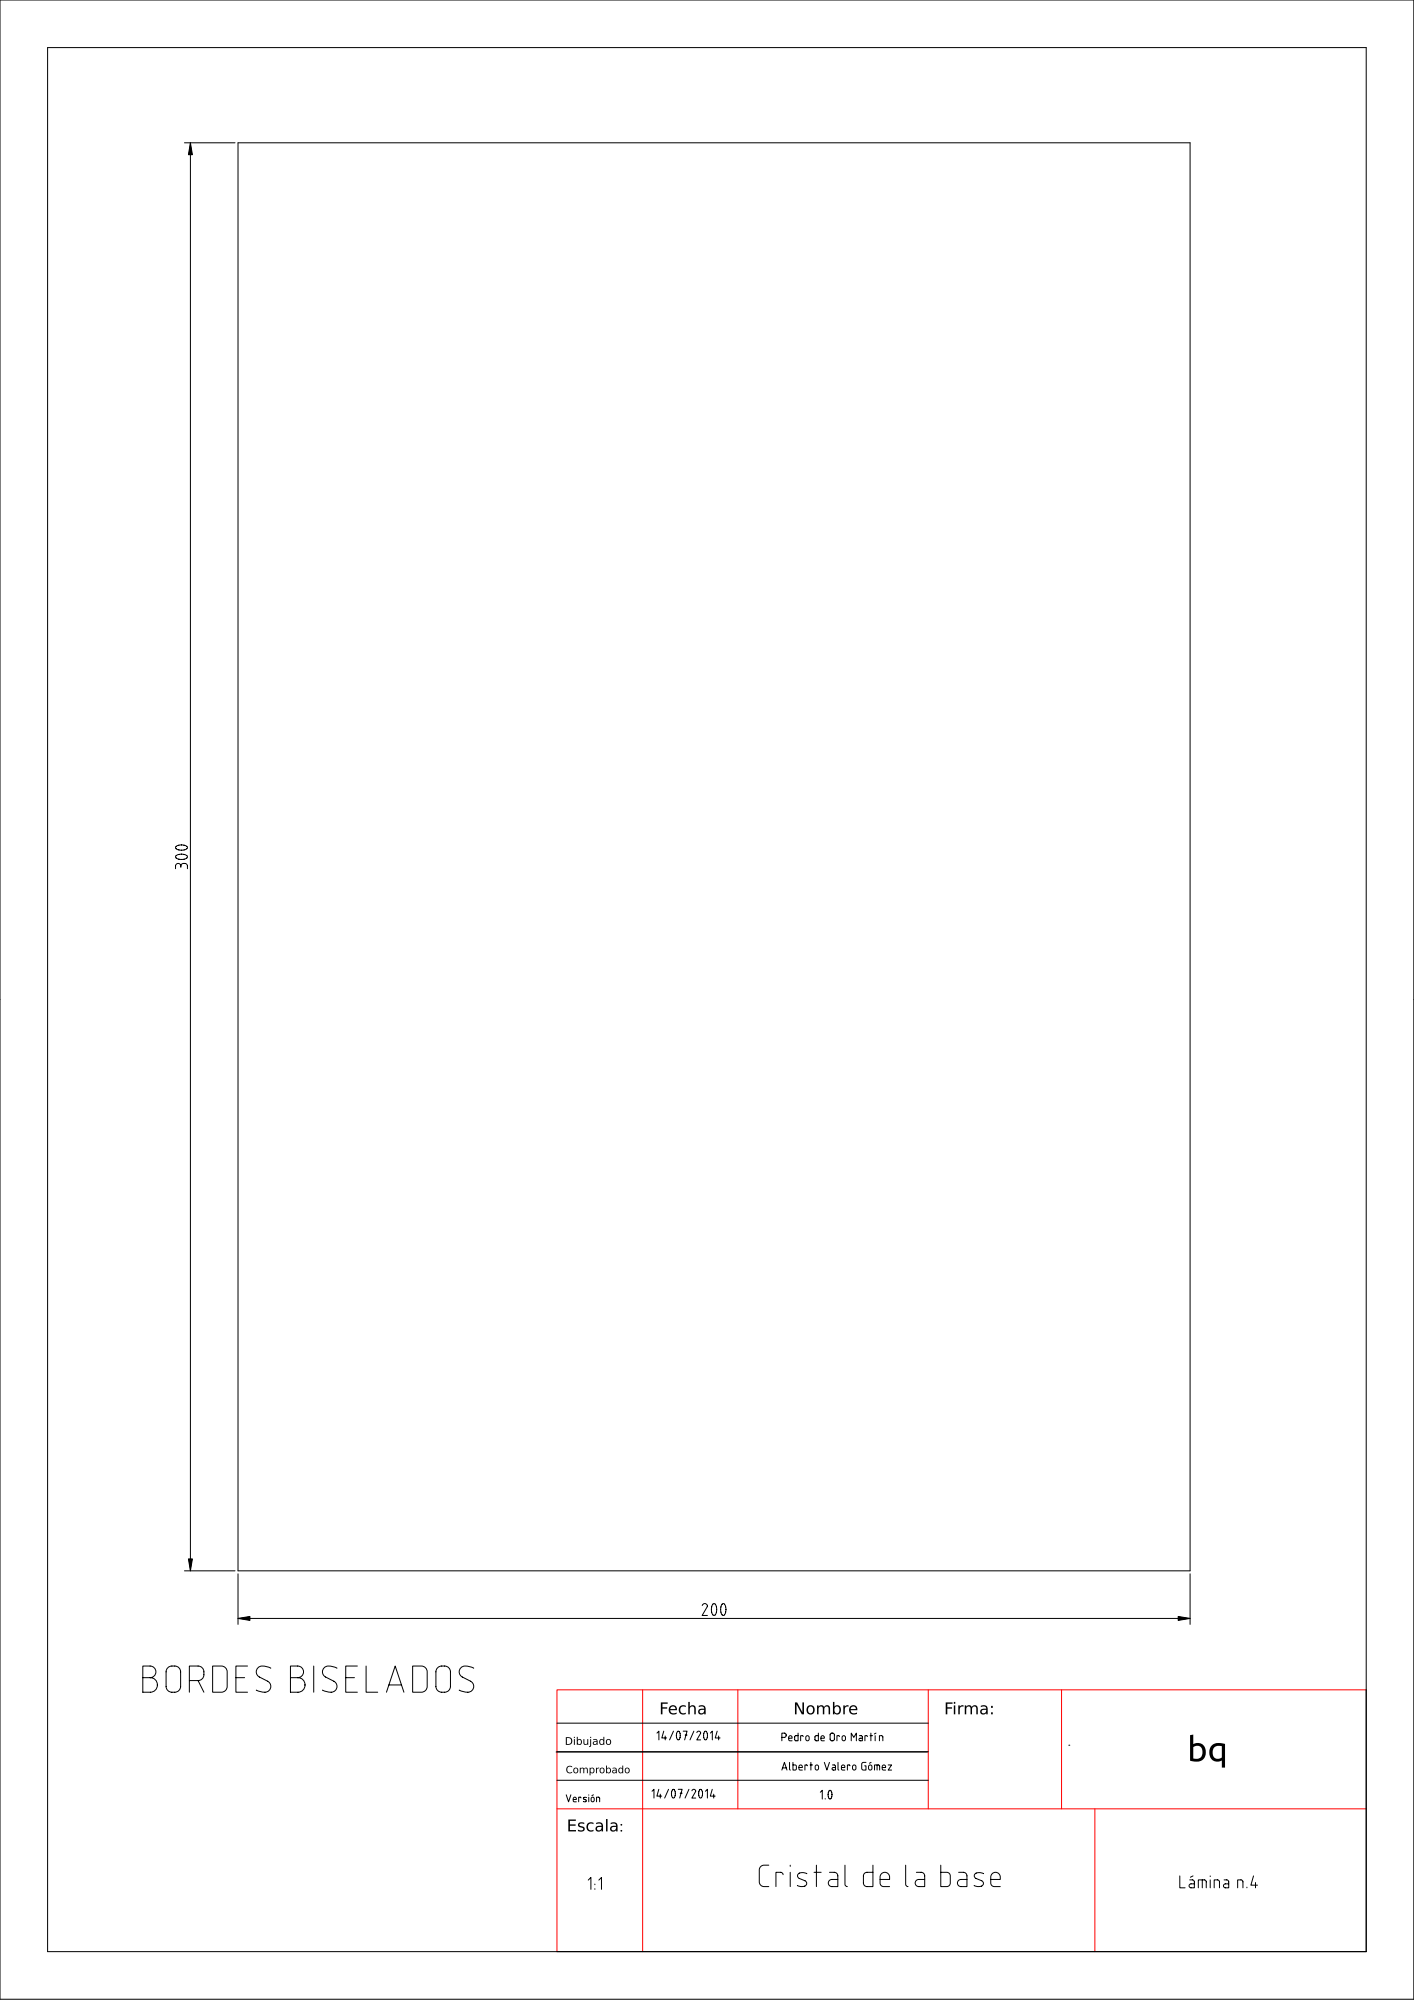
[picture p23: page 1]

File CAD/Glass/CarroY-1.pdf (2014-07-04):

1

2

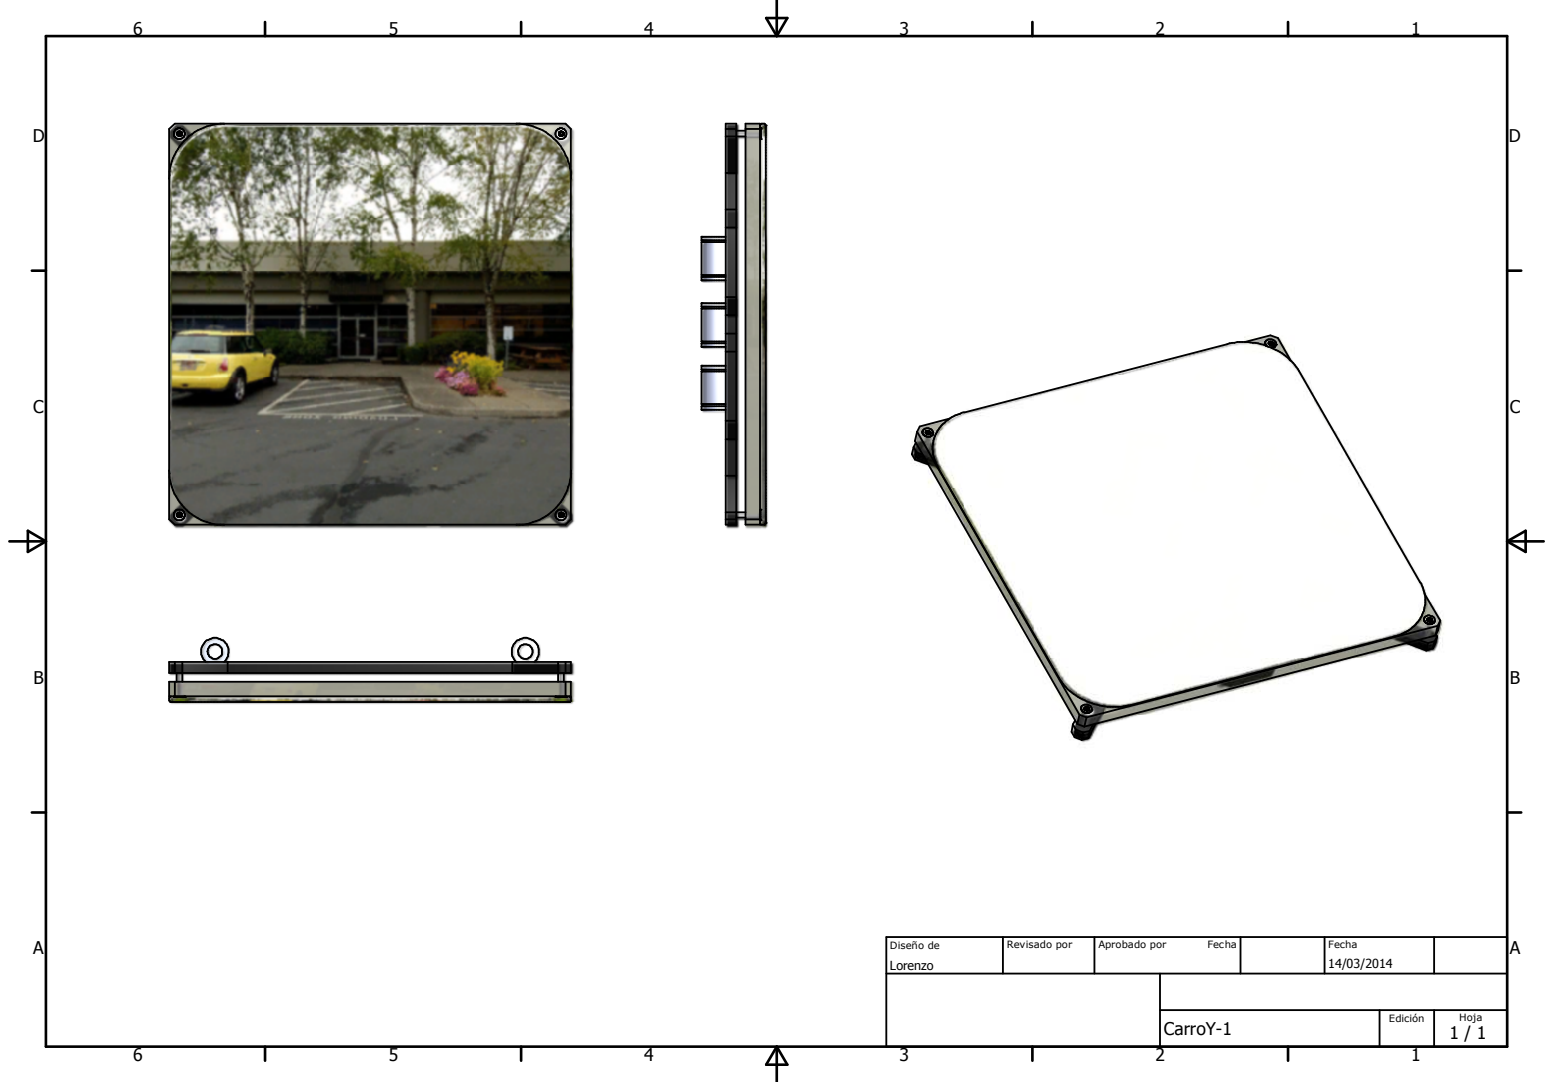
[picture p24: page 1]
CarroY-1; Lorenzo; Diseño de; Revisado por; Aprobado por; Fecha; Edición; Hoja

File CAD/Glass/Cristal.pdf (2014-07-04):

1

2

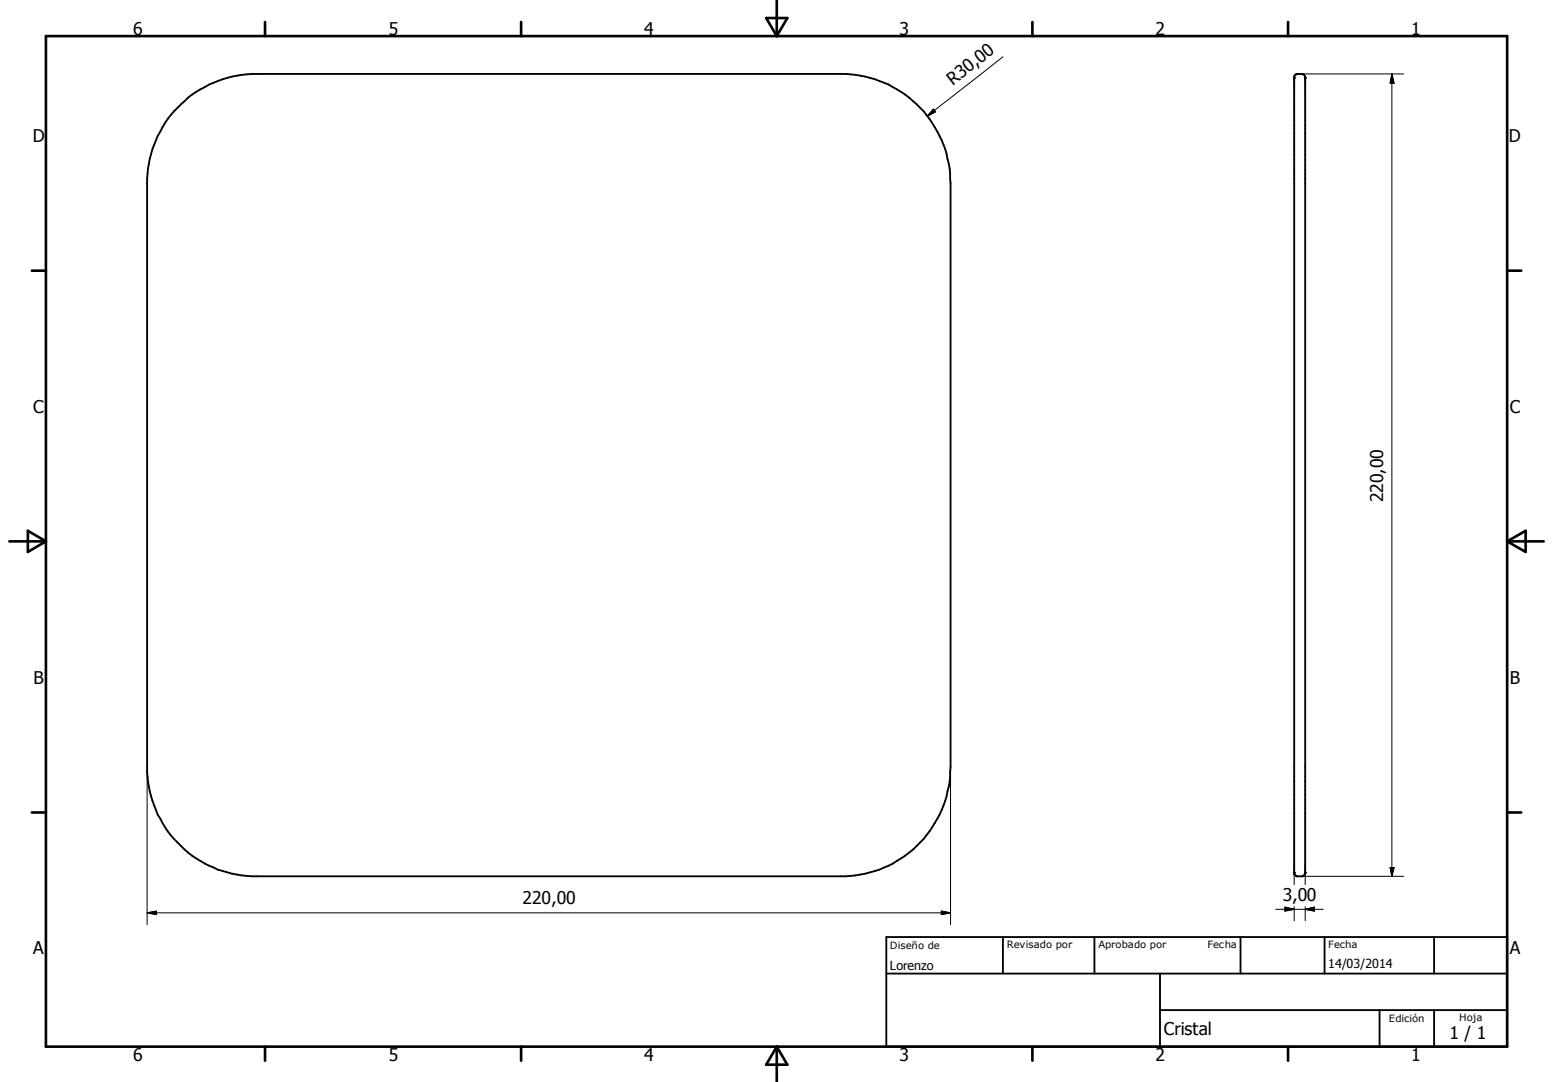
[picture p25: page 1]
Cristal; Lorenzo; Diseño de; Revisado por; Aprobado por; Fecha; Edición; Hoja

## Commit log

2014-10-13 Y corner migrated to freecad. Not yet printed
    [y-corner.stl, y-corner.stp, y-corners.fcstd]
2014-10-13 Y axis assembly (freecad). First draft
    [prusa-hephestos-assembly.fcstd]
2014-10-14 New extruder support and Frame&Base files
    [Extruder_Support_for_Prusa_i3.dxf, Extruder_Support_for_Prusa_i3_V1.stl, Extruder_Support_for_Prusa_i3_V2.stl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]
2014-10-14 y-idler-tensioner: main body and cutouts
    [y-idler-tensioner.fcstd]
2014-10-17 y-corner printed and teste. It works ok
    [y-corner.stp]
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2014-10-17 y-idler-tensioner: simple copy added
    [y-idler-tensioner.fcstd]
2014-10-17 belt guide: first draft
    [belt-guide.fcstd]
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2014-10-17 y-idler tensioner and y-belt-guide added (no screws)
    [prusa-hephestos-assembly.fcstd]
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2014-10-18 y belt guide and y-tensioner added
    [prusa-hephestos-assembly.fcstd]
2014-10-18 Belt-guide: section changed (there was a bug). Printed and test. ok
    [belt-guide.fcstd, belt-guide.stl, belt-guide.stp]
2014-10-18 assembly: finish y-tensioner and all its nuts and bolts
    [prusa-hephestos-assembly.fcstd]
2014-10-18 y-tensioner: final model. Printer and tested. ok
    [y-tensioner.stl, y-tensioner.stp]
2014-10-19 y-motor mounting plate: first draft
    [y-motor.fcstd]
2014-10-19 Prusa hephestos assembly: materials added
    [prusa-hephestos-assembly.fcstd]
2014-10-19 y-motor bracket: printed and tested. ok
    [y-motor.stl, y-motor.stp]
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2014-10-20 Cambio Y-belt sin dientes
    [EjeY_sujeta_correa.stl]
2014-10-20 Y sujeta correas sin dientes (scad)
    [EjeY_sujeta_correa.scad]
2014-10-20 Cable chain link and z-axis bottom left, by German Mira
    [cable-chain-link.fcstd, z-axis-bottom-left.fcstd]
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2014-10-24 y-belt-holder: printed and tested. OK
    [y-belt-holder.fcstd, y-belt-holder.stl, y-belt-holder.stp]
2014-10-24 y-carriage: fixed a bug in the drills
    [y-carriage.fcstd, y-carriage.stl, y-carriage.stp]
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2014-10-25 Zip ties for the y-axis, between the y-corners and the smooth rods
    [prusa-hephestos-assembly.fcstd]
2014-10-25 Zip ties for the linear bearings of the y-carriage added
    [prusa-hephestos-assembly.fcstd]
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2014-10-25 y-carriage: fixed an error on carriage dimensions
    [y-carriage.fcstd, y-carriage.stl, y-carriage.stp]
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2014-10-26 Prusa hephestos y-axis migrated to freecad. Final version with all the details
    [prusa-hephestos-assembly.fcstd]
2014-10-26 first draft of the aluminium frame. Not finished
    [frame-zy-aluminium.fcstd]
2014-10-31 y-carriage: bug fixed. Increased the distance between the linear bearing housings in 7.84mm
    [y-carriage.fcstd, y-carriage.stl, y-carriage.stp]
2014-10-31 Aluminium zx frame modelled in freecad. First draft
    [frame-zx-aluminium.fcstd, frame-zx-aluminium.stl, frame-zx-aluminium.stp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]
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2014-10-31 z-axis bottom left: exported to step and stl
    [z-axis-bottom-left.fcstd, z-axis-bottom-left.stl, z-axis-bottom-left.stp]
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2014-10-31 z axis top migrated to freecad. Left and right ends
    [z-axis-top-left.stl, z-axis-top-left.stp, z-axis-top-right.fcstd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]
2014-10-31 Prusa assembly: zx frame added with top and bottom plastic parts
    [prusa-hephestos-assembly.fcstd]
2014-10-31 z axis: M8 smooth rods and M5 threaded rods added
    [prusa-hephestos-assembly.fcstd]
2014-11-02 Endstop, modelled in Freecad by Jose Luis Villarejo
    [endstop.fcstd, endstop.stl, endstop.stp]
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2014-11-02 Eje_Y folder removed. All the stl files are in the stl folder
    [EjeY_Polea_rodamientoB623ZZ.stl, EjeY_esquina.stl, EjeY_final_carrera_base.stl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]
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2014-11-04 x-axis motor end modelled in freecad: first draft (incomplete)
    [x-axis-motor-end.fcstd]
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2014-11-05 z-endstop: distance between the drills corrected
    [z-axis-endstop.fcstd, z-axis-endstop.stl, z-axis-endstop.stp]
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2014-11-06 openscad: Code_config.scad file added. Needed for generating the x-end-idler
    [Code_Config.scad]
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2014-11-06 x-axis smooth rods: renamed in the freecad assembly file
    [prusa-hephestos-assembly.fcstd]
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2014-11-07 x-axis-idler-end: final version (not yet printed and tested)
    [x-axis-idler-end.fcstd]
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2014-11-10 z axis end stop: fixed version printed and tested
    [z-axis-endstop.stl, z-axis-endstop.stp]
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2014-11-10 x end idler. Migrated to freecad. Printed and tested
    [x-axis-idler-end.stl, x-end-idler-final.stp]
2014-11-10 x-axis belt tensioner: migrated to freecad. Printed and tested
    [x-axis-belt-tensioner.stl, x-axis-belt-tensioner.stp]
2014-11-10 x axis chain cable holder: fixed a bug. Printed and tested
    [x-axis-chain-cable-holder.stl, x-axis-chain-cable-holder.stp]
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2014-11-15 Prusa hephestos assembly: zip-tie for the x-carriage added
    [prusa-hephestos-assembly.fcstd]
2014-11-15 x-carriage: stl and step files. Not yet printed
    [x-carriage.stl, x-carriage.stp]
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2014-11-16 Prusa assembly: view changed to show the whole printer
    [prusa-hephestos-assembly.fcstd]
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2014-11-22 Reel holder migrated to freecad. stl and stp files for the left support
    [Reel-holder-left-support.fcstd, Reel-holder-supports.fcstd, reel-holder-left-support.stl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]
2014-11-22 reel holder right support: stl and stp files
    [reel-holder-right-support.stl, reel-holder-right-support.stp]
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2014-11-23 Reel holder union: stl and stp files. Printed and tested
    [reel-holder-union.stl, reel-holder-union.stp]
2014-11-23 hex key: stl and stp files. Printed and tested
    [hex-key.stl, hex-key.stp]
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2014-11-30 Bug fixed: extruder M4x20 bolts changed by M3x30. Thanks to Diego Trapero
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2014-12-06 Assembly: hotend short metal tube added
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2014-12-11 Air-nozzle freecad files moved to the witbox repos. Assembly updated
    [air-nozzle.fcstd]
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2014-12-21 Assembly: bug of the previous commit fixed
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2015-01-16 Added bed upgrade files and changed Prusa i3 Hephestos README
    [Base_metacrialto_8mm_Negro.dxf, Code_Yidler_623_modificado.scad, Code_Yidler_623_modificado.stl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]
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2015-07-01 Fixed folder name of ipt files
    [EjeX_derecha.ipt, EjeX_izquierda.ipt, EjeZ_soporte_inferior_izquierda.ipt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]
2015-08-05 Added new versions of: X Axis carriage-A V2, X Axis chain cable holder V3, Z Axis bottom left V3
    [01-Eje_X_acople_cadeneta_izquierda_v3.stl, 01-Eje_X_acople_cadeneta_izquierda_v3.stp, 14.-EjeX_carroA_v2.stl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]
